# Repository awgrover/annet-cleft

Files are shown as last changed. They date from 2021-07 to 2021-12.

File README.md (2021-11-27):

# annet-cleft

_Cleft_ is a sculpture about 8' around. 
http://www.annetcouwenberg.com/spirit

This project is meant to animate it, eventually responding to participants. 
1st animated installation (will be) at https://cadvc.umbc.edu/
Cleft has been shown before, on a static base.

Two classes at UMBC worked on the physical suspension:
http://www.annetcouwenberg.com/spirit

It has 15 segments to move. So, 15 stepper motors.
 
This project has code and electronics for the control-system.

We use a fast arduino (samd21 48MHz Zero/adafruuit-metro-m0) to get through all the floating point math in the stepper-library. Movement of the sculpture is slow, so we need less than 2 revolutions per second (<400 steps/sec). We also want more RAM for animations.

# Fritzing (wiring/electronics)

## fritzing/perf-shift-register.fzz

A perfboard layout of the current design:

* Includes place holders for stepper-driver, limit-switch, 24v power. But, those are not actual part-numbers, just place-holders.
* 1 output shift register
* 1 input shift register
* cat6 cabling
* screw-blocks for motor/limit-switch
* Controls 4 motors/limit-switches each.

We'll need 4 of these.

Plus, an arduino-to-cat6 adapter, and a final shift-out to led-bar for indicator.

The assembled system is: arduino -> perfboard -> perfboard... -> perboard w/led-bar. Going around the 8' circle (so about 24' long system).

# Arduino code

Various arduino projects in `arduino/`.

The projects share several files. Unfortunately, Windows doesn't do relative-shortcuts, and you need privileges for NTFS-links.

Thus, the same file appears to be repeated in the arduino/ projects. But, it is supposed to be the same file.

Requiring installation of a library for our common files is a complication (and synchronization issue).

So:

* Manually keep files identical
* The files are arduino/*/*.h, that appear in more than 1 directory.
* If you edit one of those, you'll need to copy it to the other places (and make sure they still work there).
* Bummer.

### 

We use SPI for talking to the shift registers because it is fast. A `.transfer(bytearray)` will write to the shift-out and simultaneously read from the shift-in. Note the stepper protocol: send the `direction` bit (w/step==low), send the leading edge of `step` (high for step, low for don't move), send the trailing-edge of `step` == low. That's 3 states (3 .transfer's), each requiring a latch pulse. Shift-in requires a latch-pulse _before_ reading.

## cleft/

The performance code. Interprets sensors, decides on animation, runs motors.

More info in `cleft.ino`.

## spi_test/

Several different modes to test the shift-in/out register setup. Use with a test jig of leds, and/or stepper-driver+motor.

See `spi_test.ino`, comments, constants, and the `loop()`.

## resource_test/

Test code for evaluating the use of arduino resources by the systems in cleft/. I used this to prove that we have enough RAM, and that each sub-system is fast enough.

# Processing code

In `processing/` :

## visualization/

A visualization of cleft. 

You can manually move each segment.

It also knows how to read the output from arduino/cleft/
and show it as a visualization of the animiation.

Uses a real simple protocol to talk to the arduino over the serial-port.

# Raspberry Pi

enable ssh, wifi to laptop hotspot, enable i2c
install arduino-cli

# enable using circuitpython libs:
sudo apt-get install -y python3-pip i2c-tools
sudo pip3 install --upgrade setuptools
pip3 install --upgrade RPi.GPIO adafruit-blinka
# pin version?
# 1st is ircam, second is mux
pip3 install adafruit-circuitpython-amg88xx adafruit-circuitpython-tca9548a
# enable user systemd service
scp -p ./pi/setup/* cleftpi.local:

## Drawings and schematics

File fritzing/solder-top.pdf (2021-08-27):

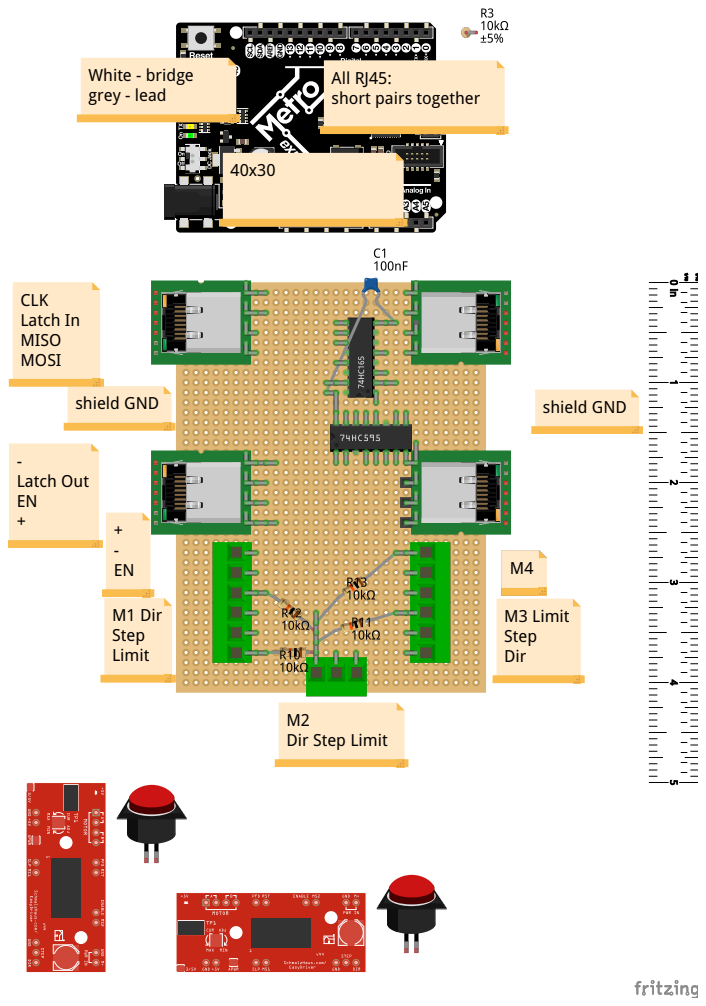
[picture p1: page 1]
M3 Limit Step Dir; M1 Dir Step Limit; shield GND; CLK Latch In MISO MOSI; - Latch Out EN +; White - bridge grey - lead

All RJ45:
short pairs together

Dir Step Limit

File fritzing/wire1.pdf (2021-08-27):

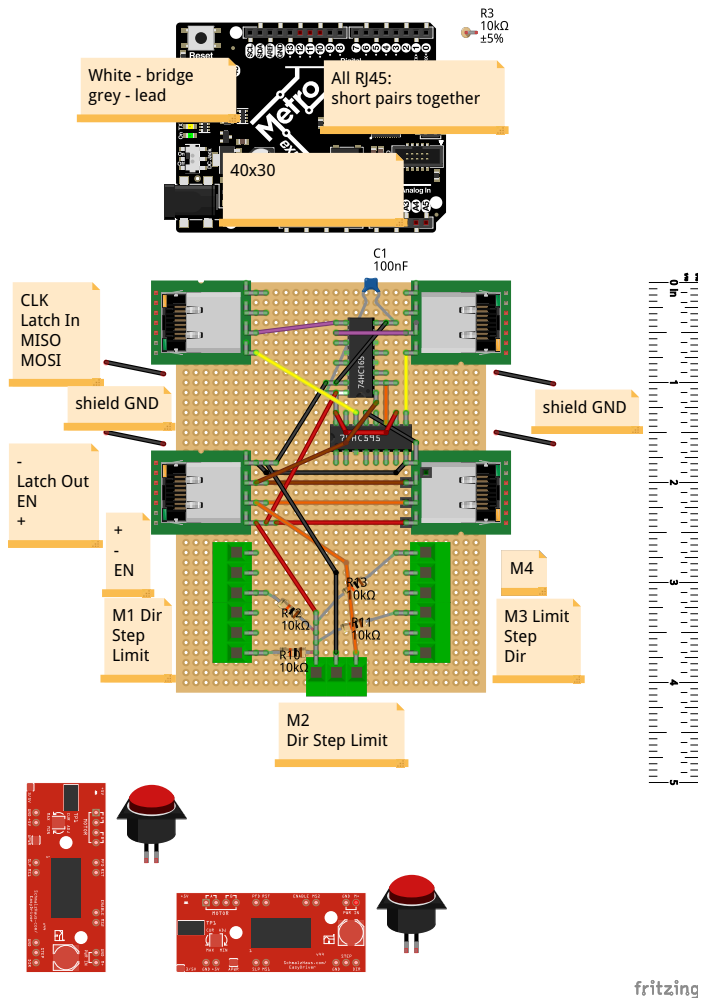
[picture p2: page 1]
CLK Latch In MISO MOSI; - Latch Out EN +; M3 Limit Step Dir; M1 Dir Step Limit; shield GND; White - bridge grey - lead

All RJ45:
short pairs together

Dir Step Limit

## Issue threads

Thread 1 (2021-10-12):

Shiftregister + Stepper Motor

beniroquai, 2021-10-12:
Hey,

I stumbled upon your code while looking for an example that enables the use of multiple steppers on an Arduino using a shift-register. May I ask you if you were able to use stepper drivers like the A4988 on the 74HC595 shift-register? Thank you ! :-)

And thank you for making the code open-source!

Best
Bene

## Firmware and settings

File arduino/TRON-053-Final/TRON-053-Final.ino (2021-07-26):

/***************************************************************************
  TRON Tech

  Designed for the UNO.

  Uses the AMG88xx GridEYE 8x8 IR camera:

  Designed specifically to work with the Adafruit AMG88 breakout
  ----> http://www.adafruit.com/products/3538
  Library "Adafruit AMG88xx Library" , dependencies not required

  These sensors use I2C to communicate. The device's I2C address is 0x69

  Written by Richard Jenkins edited by Jacob Lawler
  Copyright 2021, Richard Jenkins, Jacob Lawler
  This code is not opensource.

  IR Camera settup bassed on Writting of Dean Miller for Adafruit Industries.

 ***************************************************************************/

// Setuo for IR Camera
#include <Adafruit_AMG88xx.h> // "Adafruit AMG88xx Library", dependencies not required

// comment out to do "random" motion w/o needing the camera:
// #define USE_AMG88
// comment out to use "native"/bit-bang AccelStepper pins
#define USE_MOTORSHIELD

Adafruit_AMG88xx amg;

float oldPixels[64]; // used to compare
int dif[64];   //difference of old and new pixels

//Setup for motors
#include <AccelStepper.h> //Stepper motor Library
#ifdef USE_MOTORSHIELD
// this is using the motor shield(s)
#include <AccelStepperMotorShield.h>
Adafruit_MotorShield MotorShield1 = Adafruit_MotorShield(0x61); // shield #1
  // Make it just like a AccelStepper
AccelStepperMotorShield stepper1(
                                  MotorShield1,
                                  1, // stepper block #2
                                  SINGLE // optional/default, the stepperBlock.step-style
                                );
AccelStepperMotorShield stepper2(
                                  MotorShield1,
                                  2, // stepper block #2
                                  SINGLE // optional/default, the stepperBlock.step-style
                                );
#else
// this is "direct" bit-banging, i.e. native AccelStepper
AccelStepper stepper1(1, 4, 2);
AccelStepper stepper2(1 , 11, 7);
#endif

void setup() {
  // Setup for IR Camera
  Serial.begin(9600);

#ifdef USE_AMG88
  Serial.println(F("AMG88xx pixels"));
  bool status;
  // default settings
  status = amg.begin();
  if (!status) {
    Serial.println("Could not find a valid AMG88xx sensor, check wiring!");
    while (1);
  }

  Serial.println("-- Pixels Test --");

  Serial.println();

  delay(100); // let sensor boot up
#else
  Serial.println("Random 'zone' instead of camera\n");
#endif

  //Setup for motors
#ifdef USE_MOTORSHIELD
  stepper1.begin();
#endif
  stepper1.setMaxSpeed(2500); //Steps per seconds
  stepper1.setAcceleration(1500); //Steps/sec^2

  stepper2.setMaxSpeed(2500); //Steps per seconds
  stepper2.setAcceleration(1500); //Steps/sec^2

  Serial.println("stepper1");
  stepper1.move(50);
  stepper1.move(-50);
  Serial.println("stepper2");
  stepper2.move(50);
  stepper2.move(-50);
}


void loop() {
#ifdef USE_AMG88
  // use ir-camera:
  diff_image( oldPixels, dif);
#else
  // Don't require ir-camera, do some random motion:
  int fake_temp = 16 * random(3); // 0..2
  dif[0] = dif[16] = dif[48] = 0;
  dif[0] = 2; // has to be > 1
#endif

  /************************************
     Motor output based on IR Camera reading
   ************************************/
  // if temp increases: in top third [else], mid-third >=[16], bottom-third >=[48]
  // run the pattern for that third
  int count = 0;
  for (int i = 0; i <= 63; ++i) {
    count++;
    if (dif[i] > 1) { //Doesnt acount for drop in temp because only works with positive difference values.
      if (count >= 48) {
        // if with 3 terms
        Serial.print(millis()); Serial.print(" ");
        Serial.println("Case 1");
        stepper1.move(6500);
        stepper1.runToPosition();
        delay(10);
        stepper1.move(-6500);
        stepper1.runToPosition();
        delay(10);

        stepper2.move(6500);
        stepper2.runToPosition();
        delay(10);
        stepper2.move(-6500);
        stepper2.runToPosition();
        delay(10);
        Serial.print(millis()); Serial.print(" done\n");
        break;

      }
      else if (count >= 16) {
        Serial.print(millis()); Serial.print(" ");
        Serial.println("Case 2");
        stepper1.move(4000);
        stepper1.runToPosition();
        delay(10);
        stepper1.move(-4000);
        stepper1.runToPosition();
        delay(10);
        stepper2.move(4000);
        stepper2.runToPosition();
        delay(10);
        stepper2.move(-4000);
        stepper2.runToPosition();
        delay(10);
        Serial.print(millis()); Serial.print(" done\n");
        break;
      }

      else {
        Serial.print(millis()); Serial.print(" ");
        Serial.println("Case 3");
        stepper1.move(1500);
        stepper1.runToPosition();
        delay(10);
        stepper1.move(-1500);
        stepper1.runToPosition();
        delay(10);
        stepper2.move(1500);
        stepper2.runToPosition();
        delay(10);
        stepper2.move(-1500);
        stepper2.runToPosition();
        delay(10);
        Serial.print(millis()); Serial.print(" done\n");
        break;
      }


      Serial.println("  Movement detected");
      delay(20);
      break;
    }
    else {
      //Serial.print(count);
      Serial.println("  No Movement");
      delay(20);
    }
  }
}

void diff_image( float oldPixels[], int dif[]) {
  float pixels[64];

  /************************************
      IR Camera Image comparing
   ************************************/
  // Read values of pixels array from camera
  amg.readPixels(pixels); //Function to read variable

  //Serial.println(pixels[0]);
  //Go through each value and subtract old image by new image to find the difference
  for (int i = 0; i < 64; ++i) {
    dif[i] = pixels[i] - oldPixels[i]; // 0 is no change, positive is raised temperature of data point, and negative is drop in temperature.
    oldPixels[i] = oldPixels[i] + dif[i];
  }

  //Print difference array value for diagnosing
  Serial.print("[");
  for (int i = 1; i <= AMG88xx_PIXEL_ARRAY_SIZE; i++) {
    Serial.print(dif[i - 1]);
    Serial.print(", ");
    if ( i % 8 == 0 ) Serial.println();
  }
  Serial.println("]");
  Serial.println();
  //delay(1000);   //Delay 1 second readings
}

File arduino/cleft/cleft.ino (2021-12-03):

/*
  Interactive animation system for Cleft (Annett Couwenberg)
    cf. http://www.annetcouwenberg.com/spirit
  1st installation at https://cadvc.umbc.edu/ 2021

  The sculpture has 15 segments, roughly pie-pieces.
  Each piece has a motor attached to its outer edge,
  the inner edge being at a fixed height, and fixed to adjacent segments.
  So, it can tilt.

  Based on a sensor (initially a 8x8 ir camera),
  the segments should perform various pleasing motions.

  There is a provision for a visualization program written in processing.
  We send commands starting with "<".
  We respond to a few commands.

  Review the #define's, which change some debug & performance modes. I
  use this code in various modes (especially with the visualization) to test and develop.
  NB: AccelStepperShift.h has a relevant #define.

  In Arduino-IDE, set the Preferences:Compiler Warnings to at lease "more". Instance variable
  initiatlization order is important. We should be warning free.

  As of Nov 2021 the design is:
    one arduino Zero equivalent (48MHz): adafruit Metro M0 Express
      15 motors, with TB6600 controllers, and limit switches
      a chain of shift registers driving the controllers (SPI)
      a chain of (in) shift-registers to read the limit switches (SPI at same time)
      Several LED indicators
      AccelStepper to run the motors (but capturing as bit-vector for SPI)
    one Pi Zero
      1 IR cameras (I2C)
      python code to analyze IR camera and decide on animation
    Lots of wiring & connectors
    Not done yet:
    An animation framework based on key-frames and transition-functions.

    Wiring
      Arduino USB to Pi USB (using serial mode, and powering arduino)
      Pi : i2c pins -> i2c booster -> 3' wire -> i2c Mux -> IR Camera
      shift registers (in/out), latch-out, latch-in, stepper-enable, : see AccelStepperShift.h
      LED-Bar, end of (out) shift-register chain
        bit   assignment                          Desc
        9     Vcc "power"                         Should be on == power
        8     common-enable                       off on power-up, on at setup() and stays on
        7     spi-heartbeat (shiftreg[H]-7)       blink every 200ms, indicates spi.transfer loop being called
        6     SCK                                 looks always on during spi (actually blinks off, but imperceptible)
        5     latch-out                           very fast flash on each spi-transfer
        4     latch-in                            looks always on after spi.begin (actually blinks off, but imperceptible)
        3     recent step (shiftreg[B]-1)         on for 200ms if any motor step'd
        2     recent limit (shiftreg[C]-2)        on for 200ms if any limit switch was on
        1     spi-heartbeat (shiftreg[H']-9)      QH' (serial out) = H, slightly out of phase, blink every 200ms, indicates spi.transfer loop being called
        0     Vcc "power"                         Should be on == power

      Built-in Neopixel
        Green         power-on (def)
        Yellow        setup()
        Blink Orange  doing uplimit()
        Blink Green   loop'ing() : heartbeat
        Red           fault (past limit, or hit limit during animation)

      Neopixel 6 (center w/pentagon 5)
        spi-heartbeat -- center
        clockwise from top
        sensor
        animation state

  Several of the .h files are from my personal library of useful things:
    https://github.com/awgrover/misc_arduino_tools
  and especially a non-blocking periodic & timer:
    https://github.com/awgrover/misc_arduino_tools/blob/master/every/src/every.h
*/

#include <Adafruit_NeoPixel.h> // Adafruit
#include <AccelStepper.h> // Mike McCauley <mikem@airspayce.com>
#include <Streaming.h> // Mikal Hart <mikal@arduiniana.org>
// Not in my version of streaming, for F("") strings:
Print &operator <<(Print &obj, const __FlashStringHelper* arg) {
  obj.print(arg);
  return obj;
}

// up here so available to the #includes, which is ugly

// print position of each motor on each step if true
// If you see no steps, maybe you need the debug-jumper to fake limit switches?
// 0 = no step output
// 1 = step output on 100msec
// 2 = step output every step
// > 100 means print every n-msec
int DEBUGPOSPERSTEP = 0; // want changeable so processing can ask for steps

constexpr int MOTOR_CT = 15; // during startup, will auto detect and ignore motors whose limit is not triggered
constexpr boolean NO_EXTRA_FRAMES = false; // "true" turns off the led-indicator frame (extra shift-register).

Adafruit_NeoPixel builtin_neo(1,  40, NEO_GRB + NEO_KHZ800);
// indications for builtin neo
const uint32_t NEO_STATE_SETUP = Adafruit_NeoPixel::Color(255, 255, 0); // Yellow
const uint32_t NEO_STATE_FAULT = Adafruit_NeoPixel::Color(255, 0, 0); // Red
const uint32_t NEO_OFF = Adafruit_NeoPixel::Color(0, 0, 0); // off
const uint32_t NEO_STATE_LOOPING = Adafruit_NeoPixel::Color(0, 255, 0); // Green (blink)
const uint32_t NEO_STATE_UPLIMIT = Adafruit_NeoPixel::Color(255, 165, 0); // Orange (blink)

static boolean allow_random = true; // enable idle random animations

// NB: a #include list is magically done by arduino-ide of extant .h files
//  and it is alphabetical, so this order is not relevant
//  and, in fact, is redundant for arduino-ide
#include "freememory.h"
#include "every.h"
#include "array_size.h"
#include "ExponentialSmooth.h"
#include "AccelStepperShift.h"
#include "begin_run.h"
// #include "ArrayAnimation.h"
#include "AnimationWave1.h"
#include "AnimationTest.h"
#include "AnimationInteractive.h"

#include "Commands.h"

// if true: no initial move-to-uplimit, instead +|- move up 2, down 2
#define DEBUGMOVETEST 1
#ifndef DEBUGMOVETEST
#define DEBUGMOVETEST 0
#endif

constexpr int LATCH_PIN = 12;
constexpr int SH_LD_PIN = 11; // allow shift while high, load on low
constexpr int MOTOR_ENABLE_PIN = 10; // common stepper-driver enable
constexpr int FAKE_LIMIT_PIN = A5; // pull-up, so a jumper to A4 is "closed"
constexpr int FAKE_LIMIT_PIN_X = A4; // set to LOW, so a jumper is the "switch"

const int DISABLE_LIST[] = { -1}; /// { 5,6,9,11,0, -1 }; // 0..14, permanently not-use motors, end with -1

constexpr unsigned long ATTRACTOR_IDLE = 30UL * 1000UL; // pick an animation if we have been idle

// SYSTEMS
// Things that setup, and run during loop. See begin_run.h.
// We run them via systems[] (below)
// We need to explicitly refer to a few, so need explicit names.
// When testing/developing, you can set these to NULL to skip using them
AccelStepperShift* stepper_shift = new AccelStepperShift(
  MOTOR_CT,
  LATCH_PIN,
  SH_LD_PIN,
  MOTOR_ENABLE_PIN,
  DISABLE_LIST,
  FAKE_LIMIT_PIN,
  FAKE_LIMIT_PIN_X);
//ArrayAnimation* animation = new ArrayAnimation(MOTOR_CT); // later

AnimationWaveCute cute_wave_left( // the cute wave. sidedness is set in setup
  stepper_shift,
  5, // segments
  (AccelStepperShift::MAX_MOTION  / 2 ), // max amplitude
  0.2, // frequency
  1 // cycles
);
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

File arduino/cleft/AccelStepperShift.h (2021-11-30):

#pragma once
/*
  We want AccelStepper acceleration, etc., but we are using SPI not pins, and several steppers.

  So, subclass (class AccelStepperNoted) and note that a step is desired.

  And, have a helper (class AccelStepperShift) to collect all the stepper's desires,
  and send them out the SPI to shift registers.

  We are also reading from the shift-registers, as limit switches, so stop if we hit a limit.
*/

#include <SPI.h>

#include <AccelStepper.h> // Mike McCauley <mikem@airspayce.com>
#include <Streaming.h> // Mikal Hart <mikal@arduiniana.org>

#include "freememory.h"
#include "every.h"
#include "begin_run.h"

// true to print "done" everytime all motors finish
// probably too noisy when running a real pattern
#define DEBUGDONERUN 1


// the COUNT of motors to debug, stops after that
//  undef or -1 is don't,
//#define DEBUGBITVECTOR 0
// 1 to print the bit-vector every time
// 2 to print on "blink"
// 3 to print limit-switch-bit-vector on shift-out
// 4 to print all bit-vectors( step, dir, limit)
#define DEBUGLOGBITVECTOR 0
// stop run()'ing after this number of steps, 0 means don't stop
//#define DEBUGSTOPAFTER 2
// print calcalation for frame[i] = value & mask
///#define    DEBUGFRAME 1
// Delay between each shift
//#define DEBUGSTUPIDSLOW 500

#ifndef DEBUGDONERUN
#define DEBUGDONERUN 0
#endif
#ifndef DEBUGBITVECTOR
#define DEBUGBITVECTOR -1
#endif
#ifndef DEBUGLOGBITVECTOR
#define DEBUGLOGBITVECTOR 0
#endif

#ifndef DEBUGSTOPAFTER
#define DEBUGSTOPAFTER 0
#endif
#ifndef DEBUGFRAME
#define DEBUGFRAME 0
#endif
#ifndef DEBUGSTUPIDSLOW
#define DEBUGSTUPIDSLOW 0
#endif

class AccelStepperNoted: public AccelStepper {
    // This class just notes that a step is requested.
    // A user of the instance should reset `do_step` once it is read.
    // Need to call the usual .runX(), and other .setX() as normal.
    // NB: the last step() will have .run() return false, so use do_step():
    //  amotor.run();
    //  if (amotor.do_step) { handle it, set do_step=false ...}

  public:
    inline boolean direction() {
      return _direction;  // expose, true == foward
    }

    const int motor_i; // my index

    boolean do_step; // true == do a step, reset after this is used
    boolean at_limit = false; // triggered by limit_switch detection during home-to-up-limit
    int at_limit_pos = 0; // where the limit switch was last triggered (we can decel past this).

    // this super's constructor causes no use of pins
    // "enable" is common to all motors at once.
    AccelStepperNoted(int i) : AccelStepper(&dumyStep, &dumyStep) , motor_i(i), do_step(false) {}
    static void dumyStep() {}

    void step(long astep) {
      // step is just current position
      // we just note that a step is requested
      (void)(astep); // Unused

      if (DEBUGPOSPERSTEP == 2) Serial << F("<P ") << motor_i << F(" ") << currentPosition() << endl;
      do_step = true;
    }

    int time_to(int position, float acceleration ) { // OMG private var again
      // how many microseconds
      // just an estimate, not good for short distances
      int distance = abs(position - currentPosition());
      int ms = int( 1000.0 * distance / maxSpeed() );
      //Serial << F("time_to ") << position << F(" from ") << currentPosition() << F(" dist ") << distance << F(" ms ") << ms << endl;
      return ms ;

      // d= 1/2 a t^2
      // 2d = a t^2
      // 2d/a = t^2
      // sqrt(2d/a) = t
      // BUT, we want to to accel half-way, then decl, so the `distance` is 1/2, and the time is *2
      //int ms =  int( 2 * sqrt( distance / acceleration ) * 1000 ); // sec to msec
      //Serial << F("time_to ") << position << F(" from ") << currentPosition() << F(" dist ") << distance << F(" @ accel ") << acceleration << F(" ms ") << ms << endl;
      //return ms ;
    }
};

class AccelStepperShift : public BeginRun {
    // for many DFRobot TB6600
    //    input labeling seems confusing, all "+" to +,
    //      pul- steps on transition to high.
    //      dir- : high is forward, low is backwards (clock/counter-clock).
    // via a chain of shift-registers (2 bits per tb6600, common enable)
    //  74HC595 is serial-to-parallel: output on latch going high
    //  74HC165 is parallel-to-serial: input on latch going low (before read)
    //    nb: opposite sense of latch from the 595
    //    we are doing MSBFIRST, so 165's bits are reversed: A is [7]
    //  Wiring: Arduino   Shift-Register 74HC595  tb6600          Shift-register 74HC165
    //          3.3V      16 VCC 3V               dir+,pul+,en+   16 Vcc
    //          GND       8 GND                                   8 GND
    //          MOSI      14 SER (shiftin)
    //          MISO                                              9 Qh (shiftout) (7 is ~Qh)
    //          SCK       11 SRCLK                                2 clk (15 & 2 can be swapped)
    //          latch_pin 12 RCLK
    //          load-pin                                          1 SH/~LD (latch - read on low, high for shift)
    //                    13 ~OE pull low
    //                    10 ~SRCLR pull high
    //                    9 q7'/data-out -> SER
    //                    15 q0                   motor0 dir-
    //                    1 q1                    motor0 pul- (step)
    //                    q2/q3                   motor1, ...
    //                                                            11 A limit1
    //                                                            13 C limit2, 3 E limit 3, 5 G limit 4
    //                                                            11,12,13,14, 3,4,5,6 Do not let them float. pull low if not used
    //                                                            15 clk-inh, pull low
    //                                                            10 SER shiftin daisy chain to 9 Qh, pull low on last
    //          GND
    //          motor-enable                      en- (HIGH for engage, low for free), pull low
    //
    //  5MHz clock max at 2v, 25MHz at 5v, so... at 3v...
    //  20mA max per output (?)
    //
    // To test for acceleration
    //    Set the driver to a very small current so the motor will slip (maybe 0.5A).
    //    Test various accelerations till no slip
    //    Set the driver back to operating current
    //
    // Indicators
    //    SCK is too fast to see (only on for about 60micros!)
    //    mosi gets left on, so not useful
    //    data doesn't even seem to change!
    // using an AccelStepper per motor
    //
    // This class
    // * constructs AccelStepperNoted per motor
    // * has run() to run all motors
    // * converts the "noted" steps into bit-vectors for fast spi-shift out
    //    to drive the tb6600's
    // * reads the limit switches
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

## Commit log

2021-07-19 allow camera disable
2021-07-24 building up arduino
2021-07-26 cleft_arduino compiles, building up framework
2021-07-30 resource/feasibility test so far. start accel-stepper-shift
2021-07-30 resource test for all motors shifting out
2021-07-31 debugged shift, do led-bar
2021-07-31 use spi-begintransaction
2021-07-31 fix a warning. calculate accel
    [AccelStepperShift.h]
2021-07-31 do goto to limit and handle limit switches
2021-08-01 replace Beastie with BeginRun
    [AccelStepperShift.h]
2021-08-01 organize into arduino/ and processing/ dirs
2021-08-05 use correct latch pin
    [AccelStepperShift.h, cleft.ino]
2021-08-06 fix multiple animation. start wave2
    [AccelStepperShift.h, AnimationWave1.h, Commands.h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]
2021-08-09 +- command in arduino code
2021-08-09 reworking order of bytes in bit-vector shift
    [AccelStepperShift.h]
2021-08-09 fix shift, etc.. motor0 works\!
    [AccelStepperShift.h, Commands.h]
2021-08-11 other arduino and fritzing
    [breadboard-shift-register.fzz, wiring-layout.fzz]
2021-08-13 update wiring
2021-08-14 update pin wiring
2021-08-16 change to reading limit-switch bit-vector
2021-08-16 dump limit switch read
2021-08-16 add more wiring commments. use HIGH/LOW. add enable_pin. add heartbeat and recent-step to led-bar.
2021-08-16 testing led bar
2021-08-16 using only 2 shift-registers, led-bar blink
2021-08-16 clean up led-bar on expiry
2021-08-17 add perfboard layout
    [perf-shift-register.fzz]
2021-08-18 cleanup the wiring. comment spi_test.ino
    [perf-shift-register.fzz]
2021-08-20 adding wiring test to spi-test
    [perf-shift-register.fzz]
2021-08-20 refine wiring
    [perf-shift-register.fzz]
2021-08-22 perboard image
    [perf-shift-register.fzz]
2021-08-27 xsl filters
2021-08-28 rework serial begin. more comments
    [cleft.ino]
2021-09-04 fix limit-switch detect
2021-09-17 add ignore-limit-switch
2021-09-18 global all_done, allow_random. disable goto_limit on jumper. factor Animation.h, add motor tests. add idle animation.
2021-09-26 fix comments. library version of every.
    [AnimationTest.h, cleft.ino]
2021-09-30 fix steps per meter
    [AccelStepperShift.h, cleft.ino]
2021-09-30 fixing usable motor logic
    [AccelStepperShift.h, cleft.ino]
2021-10-31 add ir camera visualizer
2021-11-17 add histo, 1st draft finding heat island
2021-11-18 histo temps, printing, display temps
2021-11-24 fix background calc, fix firsthigh calc
    [ircam.py]
2021-11-26 hotspot located right: inverted not mirrored. minmax doing i,temp,x,y. start hotspot. processing using minmax
    [ir_camera.pde, ircam.py]
2021-11-27 tweak glitch temp in Background. rework hotspot. fix choose-animation. fix exponential_smooth. processing read and render hotspot/animation. reduce verbosity.
    [ir_camera.pde, ircam.py]
2021-11-27 add basic arduino send animation number
2021-11-27 warmup for arduino
2021-11-30 rework worn/breathing. move DEBUGPOSPERSTEP and make a dynamic setting. move around some status messages. add status messages for some animations.
    [AccelStepperShift.h, AnimationInteractive.h, AnimationWave1.h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]
2021-11-30 jitter decays and stops. ircam.py uses a file for send_animation, and has warmup time
    [AnimationInteractive.h, cleft.ino, ircam.py]
